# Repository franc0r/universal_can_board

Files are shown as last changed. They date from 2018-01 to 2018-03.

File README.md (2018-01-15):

# universal_can_board
Contains schematic, pcb layout and software of the francor's universal can board.

# Description
The universal board is used to control and monitor several components of a mobile robot like the motor controllers, co2 sensors, pan tilt unit, etc...

The board communicates via CAN interface. The used µC is a AVR from the Arduino Nano v2. Future more this board is based on an Arduino, so the Arduino IDE can be used to programm the board.

# Requirements
## Motor Controller
The BLD300B motor controller is used to drive the Robot Morty. This controller must be controlled and monitored by the board. For this following inputs and outputs are required.

* Input
  * An analog to measure current voltage of the motor controller.
  * An analog to measure current current of the motor controller.
  * Three digital to get the hall sensors of the hub motor wheels.
  * An digital to get the speed ticks from the motor controller.
* Output
  * An PWM to set the motor power.
  * An digital to set the rotation direction.
  * An digital to enable/disable the break.
  * An digital to enable/disable the motor controller.
  
## CO2 Sensor
The universal board should be able to measure the CO2 sensor and publish the values via CAN.

* Input
  * An analog to measure the current CO2 concentration.
  
* Output
  * An digital to indicate a high CO2 concentration. (drive a LED).

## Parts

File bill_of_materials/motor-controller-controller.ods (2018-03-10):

IC1 | ATMEGA328P-A | TQFP32 | https://www.reichelt.de/?ARTICLE=121830&PROVID=2788 | 1,4
U1 | FT232RL | SSOP28 | https://www.reichelt.de/?ACTION=3;ARTICLE=64399;SEARCH=ft232rl | 3,6
U2 | LM1117-5.0 | SOT-223 | https://www.reichelt.de/?ACTION=3;ARTICLE=109330;SEARCH=lm1117 | 0,86
U3 | MCP2515 | TSSOP-20 | https://www.reichelt.de/?ACTION=3;ARTICLE=168468;SEARCH=mcp2515 | 2,15
U4 | MCP2551 | SOIC-8 | https://www.reichelt.de/?ACTION=3;ARTICLE=90069;SEARCH=mcp2551 | 1,25
D4 | B2100-13-F | SMB | https://www.reichelt.de/?ACTION=3;ARTICLE=216722;SEARCH=b2100-13 | 0,28
D13 | B2100-13-F | SMB | https://www.reichelt.de/?ACTION=3;ARTICLE=216722;SEARCH=b2100-13 | 0,28
D14 | B2100-13-F | SMB | https://www.reichelt.de/?ACTION=3;ARTICLE=216722;SEARCH=b2100-13 | 0,28
P1 | USB Mini B | USB_OTG | https://www.reichelt.de/USB-Einbauverbinder/USB-BWM-SMD/3/index.html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 | 0,28
Y1 | Quarz 16MHz | 3x5 mm | https://www.reichelt.de/Quarze-SMD-Keramikgehaeuse/16-000000-MJ/3/index.html?ACTION=3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 | 0,9
Y2 | Quarz 16MHz | 3x5 mm | https://www.reichelt.de/Quarze-SMD-Keramikgehaeuse/16-000000-MJ/3/index.html?ACTION=3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 | 0,9
C21 | 10u 16V | 1210 | https://www.reichelt.de/Vielschicht-SMD-G1210/KEM-Y5V1210-10U/3/index.html?ACTION=3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 | 0,16
C1 | 100nF | 805 | https://www.reichelt.de/Vielschicht-SMD-G0805/KEM-X7R0805-100N/3/index.html?ACTION=3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 | 0,02
C3 | 100nF | 805 | https://www.reichelt.de/Vielschicht-SMD-G0805/KEM-X7R0805-100N/3/index.html?ACTION=3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 | 0,02
C4 | 100nF | 805 | https://www.reichelt.de/Vielschicht-SMD-G0805/KEM-X7R0805-100N/3/index.html?ACTION=3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 | 0,02
C5 | 100nF | 805 | https://www.reichelt.de/Vielschicht-SMD-G0805/KEM-X7R0805-100N/3/index.html?ACTION=3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 | 0,02
C6 | 100nF | 805 | https://www.reichelt.de/Vielschicht-SMD-G0805/KEM-X7R0805-100N/3/index.html?ACTION=3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 | 0,02
C22 | 100nF | 805 | https://www.reichelt.de/Vielschicht-SMD-G0805/KEM-X7R0805-100N/3/index.html?ACTION=3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 | 0,02
C23 | 100nF | 805 | https://www.reichelt.de/Vielschicht-SMD-G0805/KEM-X7R0805-100N/3/index.html?ACTION=3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 | 0,02
C24 | 100nF | 805 | https://www.reichelt.de/Vielschicht-SMD-G0805/KEM-X7R0805-100N/3/index.html?ACTION=3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 | 0,02
C25 | 100nF | 805 | https://www.reichelt.de/Vielschicht-SMD-G0805/KEM-X7R0805-100N/3/index.html?ACTION=3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 | 0,02
C26 | 100nF | 805 | https://www.reichelt.de/Vielschicht-SMD-G0805/KEM-X7R0805-100N/3/index.html?ACTION=3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 | 0,02
C27 | 100nF | 805 | https://www.reichelt.de/Vielschicht-SMD-G0805/KEM-X7R0805-100N/3/index.html?ACTION=3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 | 0,02
C9 | 4u7 | 1210 | https://www.reichelt.de/Vielschicht-SMD-G1210/KEM-X7R1210-4-7U/3/index.html?ACTION=3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 | 0,28
C20 | 4u7 | 1210 | https://www.reichelt.de/Vielschicht-SMD-G1210/KEM-X7R1210-4-7U/3/index.html?ACTION=3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 | 0,28
D5 | BAT54S | SOT-23 | https://www.reichelt.de/BA-BAY-BB-Dioden/BAT-54S-SMD/3/index.html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 | 0,04
D6 | BAT54S | SOT-23 | https://www.reichelt.de/BA-BAY-BB-Dioden/BAT-54S-SMD/3/index.html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 | 0,04
D7 | BAT54S | SOT-23 | https://www.reichelt.de/BA-BAY-BB-Dioden/BAT-54S-SMD/3/index.html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 | 0,04
D8 | BAT54S | SOT-23 | https://www.reichelt.de/BA-BAY-BB-Dioden/BAT-54S-SMD/3/index.html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 | 0,04
D9 | BAT54S | SOT-23 | https://www.reichelt.de/BA-BAY-BB-Dioden/BAT-54S-SMD/3/index.html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 | 0,04
D10 | BAT54S | SOT-23 | https://www.reichelt.de/BA-BAY-BB-Dioden/BAT-54S-SMD/3/index.html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 | 0,04
D11 | BAT54S | SOT-23 | https://www.reichelt.de/BA-BAY-BB-Dioden/BAT-54S-SMD/3/index.html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 | 0,04
D12 | BAT54S | SOT-23 | https://www.reichelt.de/BA-BAY-BB-Dioden/BAT-54S-SMD/3/index.html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 | 0,04
R7 | 220R | 805 | https://www.reichelt.de/SMD-0805-von-0-bis-910-Ohm/SMD-0805-220/3/index.html?ACTION=3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 | 0,03
R8 | 220R | 805 | https://www.reichelt.de/SMD-0805-von-0-bis-910-Ohm/SMD-0805-220/3/index.html?ACTION=3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 | 0,03
R9 | 220R | 805 | https://www.reichelt.de/SMD-0805-von-0-bis-910-Ohm/SMD-0805-220/3/index.html?ACTION=3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 | 0,03
R10 | 220R | 805 | https://www.reichelt.de/SMD-0805-von-0-bis-910-Ohm/SMD-0805-220/3/index.html?ACTION=3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 | 0,03
R11 | 220R | 805 | https://www.reichelt.de/SMD-0805-von-0-bis-910-Ohm/SMD-0805-220/3/index.html?ACTION=3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 | 0,03
R12 | 220R | 805 | https://www.reichelt.de/SMD-0805-von-0-bis-910-Ohm/SMD-0805-220/3/index.html?ACTION=3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 | 0,03
R13 | 220R | 805 | https://www.reichelt.de/SMD-0805-von-0-bis-910-Ohm/SMD-0805-220/3/index.html?ACTION=3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 | 0,03
R14 | 220R | 805 | https://www.reichelt.de/SMD-0805-von-0-bis-910-Ohm/SMD-0805-220/3/index.html?ACTION=3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 | 0,03
R1 | 1k | 805 | https://www.reichelt.de/SMD-0805-von-1-bis-910-kOhm/RND-0805-5-5-1K/3/index.html?ACTION=3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 | 0,02
R2 | 1k | 805 | https://www.reichelt.de/SMD-0805-von-1-bis-910-kOhm/RND-0805-5-5-1K/3/index.html?ACTION=3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 | 0,02
R3 | 1k | 805 | https://www.reichelt.de/SMD-0805-von-1-bis-910-kOhm/RND-0805-5-5-1K/3/index.html?ACTION=3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 | 0,02
R4 | 1k | 805 | https://www.reichelt.de/SMD-0805-von-1-bis-910-kOhm/RND-0805-5-5-1K/3/index.html?ACTION=3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 | 0,02
R5 | 1k | 805 | https://www.reichelt.de/SMD-0805-von-1-bis-910-kOhm/RND-0805-5-5-1K/3/index.html?ACTION=3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 | 0,02
R6 | 1k | 805 | https://www.reichelt.de/SMD-0805-von-1-bis-910-kOhm/RND-0805-5-5-1K/3/index.html?ACTION=3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 | 0,02
R15 | 1k | 805 | https://www.reichelt.de/SMD-0805-von-1-bis-910-kOhm/RND-0805-5-5-1K/3/index.html?ACTION=3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 | 0,02
R16 | 120R | 805 | https://www.reichelt.de/SMD-0805-von-0-bis-910-Ohm/SMD-0805-120/3/index.html?ACTION=3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 | 0,03

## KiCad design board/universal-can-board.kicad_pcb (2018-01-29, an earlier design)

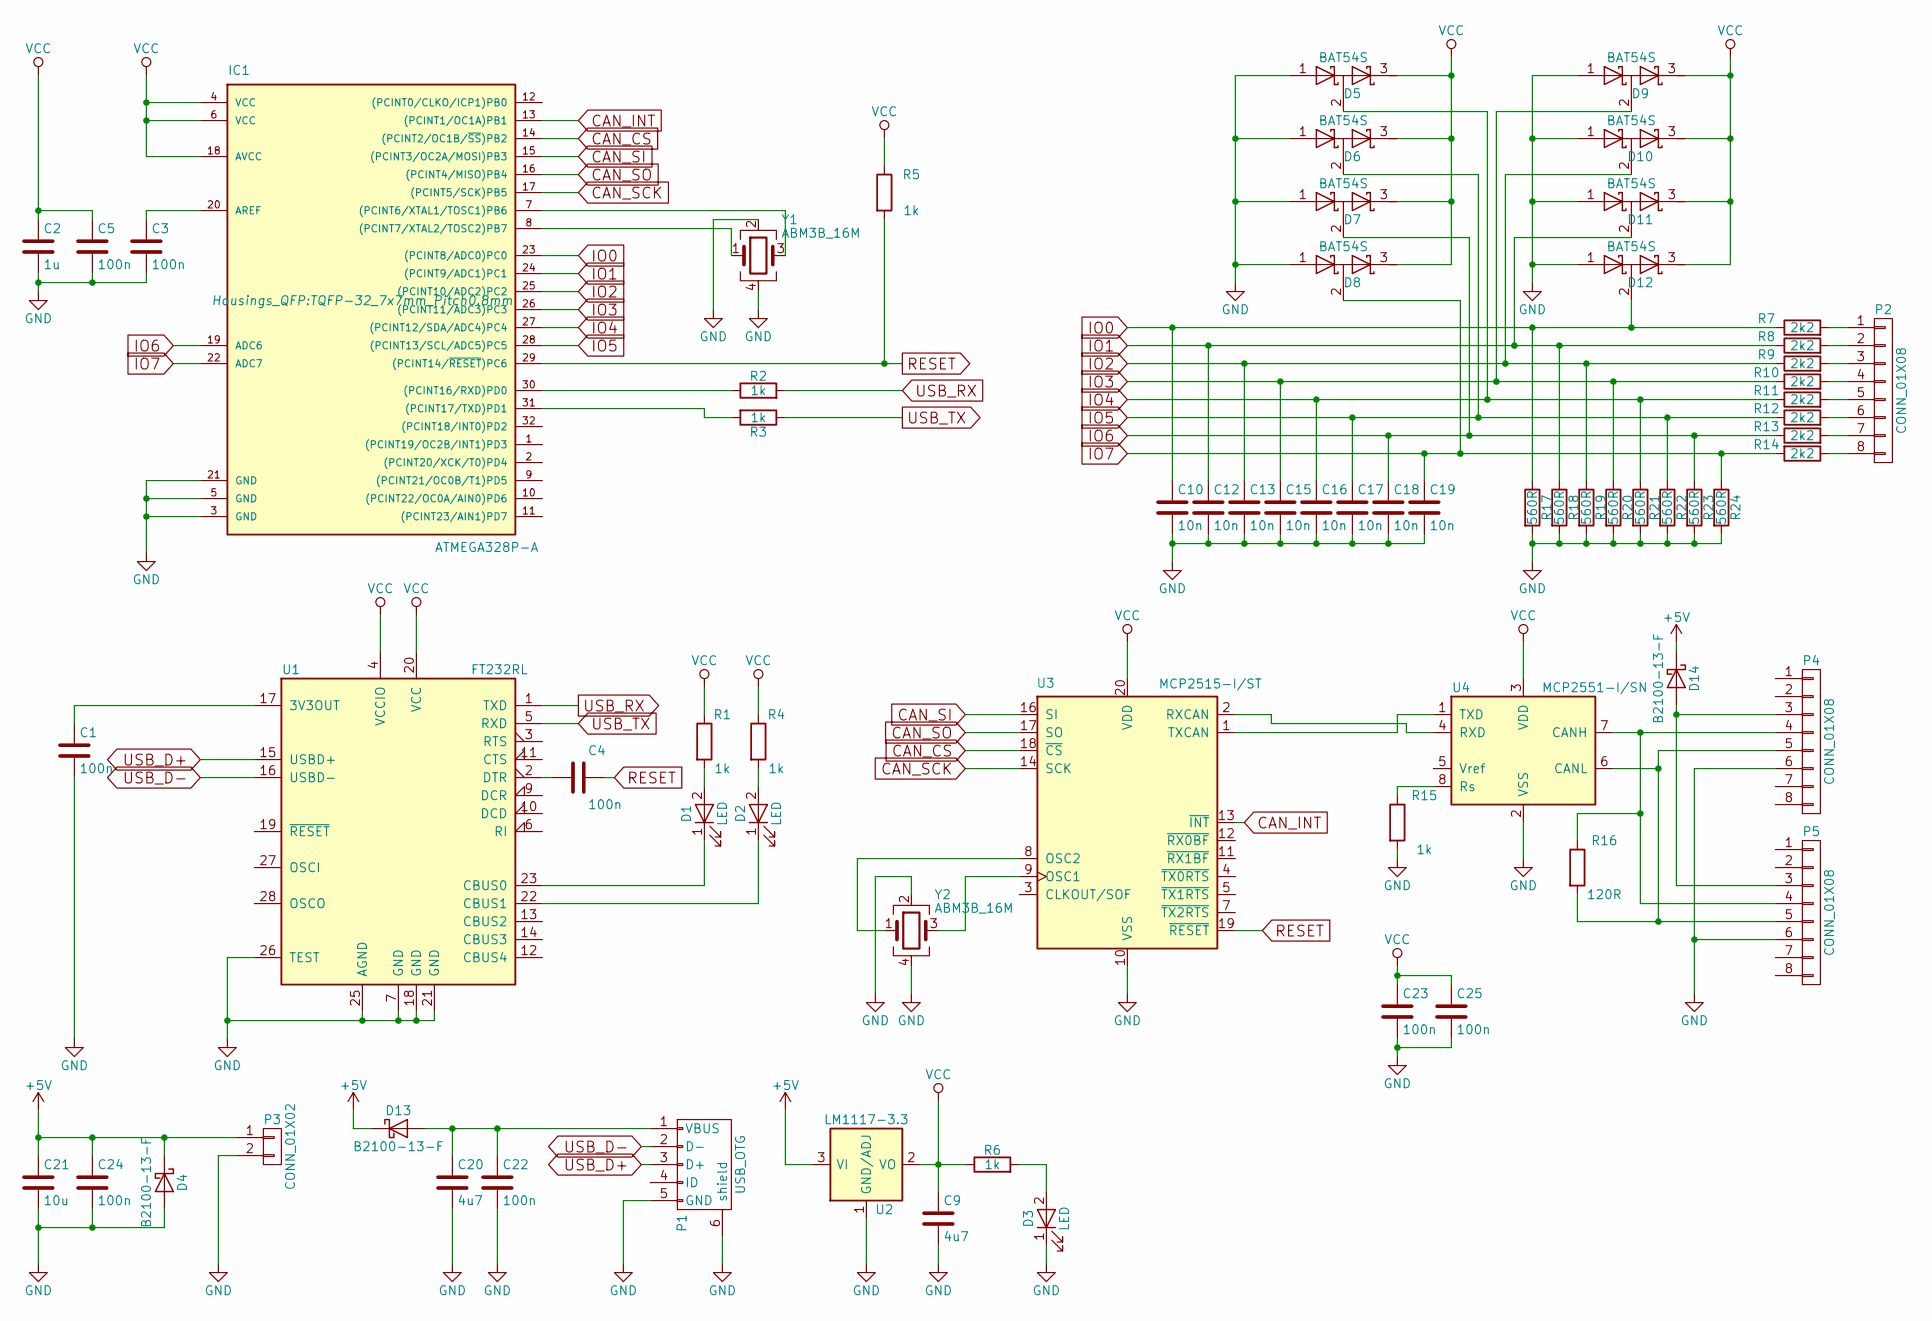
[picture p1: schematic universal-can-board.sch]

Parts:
C1, C3, C4, C5, C22, C23, C24, C25: 100n; C_0805
C2: 1u; C_0805
C9, C20: 4u7; C_1210
C10, C12, C13, C15, C16, C17, C18, C19: 10n; C_0805
C21: 10u; C_1210
D1, D2, D3: LED; LED_0805
D4, D13, D14: B2100-13-F; SMB_Standard
D5, D6, D7, D8, D9, D10, D11, D12: BAT54S; SOT-23
IC1: ATMEGA328P-A; TQFP-32_7x7mm_Pitch0.8mm
P1: USB_OTG; USB_Mini-B_Lumber_2486_Horizontal
P2: CONN_01X08; PhoenixContact_MSTBVA-G_08x5.08mm_Vertical
P3: CONN_01X02; PhoenixContact_MSTBVA-G_02x5.08mm_Vertical
P4, P5: CONN_01X08; RJ45_8
R1, R2, R3, R4, R5, R6, R15: 1k; R_0805
R7, R8, R9, R10, R11, R12, R13, R14: 2k2; R_0805
R16: 120R; R_0805
R17, R18, R19, R20, R21, R22, R23, R24: 560R; R_0805
U1: FT232RL; SSOP-28_5.3x10.2mm_Pitch0.65mm
U2: LM1117-3.3; SOT-223
U3: MCP2515-I/ST; TSSOP-20_4.4x6.5mm_Pitch0.65mm
U4: MCP2551-I/SN; SOIC-8_3.9x4.9mm_Pitch1.27mm
Y1, Y2: ABM3B_16M; Crystal_SMD_5032_4Pads

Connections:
+5V: C21.1, C24.1, D4.1 (K), D13.1 (K), D14.1 (K), P3.1, U2.3 (VI)
CAN_CS: IC1.14 ((PCINT2/OC1B/~SS~)PB2), U3.18 (~CS)
CAN_INT: IC1.13 ((PCINT1/OC1A)PB1), U3.13 (~INT)
CAN_SCK: IC1.17 ((PCINT5/SCK)PB5), U3.14 (SCK)
CAN_SI: IC1.15 ((PCINT3/OC2A/MOSI)PB3), U3.16 (SI)
CAN_SO: IC1.16 ((PCINT4/MISO)PB4), U3.17 (SO)
GND: C1.2, C2.2, C3.2, C5.2, C9.2, C10.2, C12.2, C13.2, C15.2, C16.2, C17.2, C18.2, C19.2, C20.2, C21.2, C22.2, C23.2, C24.2, C25.2, D3.1 (K), D4.2 (A), D5.1 (A), D6.1 (A), D7.1 (A), D8.1 (A), D9.1 (A), D10.1 (A), D11.1 (A), D12.1 (A), IC1.3 (GND), IC1.5 (GND), IC1.21 (GND), P1.5 (GND), P1.6 (shield), P3.2, P4.6, P5.6, R15.2, R17.2, R18.2, R19.2, R20.2, R21.2, R22.2, R23.2, R24.2, U1.7 (GND), U1.18 (GND), U1.21 (GND), U1.25 (AGND), U1.26 (TEST), U2.1 (GND/ADJ), U3.10 (VSS), U4.2 (VSS), Y1.2, Y1.4, Y2.2, Y2.4
IO0: C10.1, D12.2 (common), IC1.23 ((PCINT8/ADC0)PC0), R7.1, R17.1
IO1: C12.1, D11.2 (common), IC1.24 ((PCINT9/ADC1)PC1), R8.1, R18.1
IO2: C13.1, D10.2 (common), IC1.25 ((PCINT10/ADC2)PC2), R9.1, R19.1
IO3: C15.1, D9.2 (common), IC1.26 ((PCINT11/ADC3)PC3), R10.1, R20.1
IO4: C16.1, D5.2 (common), IC1.27 ((PCINT12/SDA/ADC4)PC4), R11.1, R21.1
IO5: C17.1, D6.2 (common), IC1.28 ((PCINT13/SCL/ADC5)PC5), R12.1, R22.1
IO6: C18.1, D7.2 (common), IC1.19 (ADC6), R13.1, R23.1
IO7: C19.1, D8.2 (common), IC1.22 (ADC7), R14.2, R24.1
unnamed: C1.1, U1.17 (3V3OUT)
unnamed: C3.1, IC1.20 (AREF)
unnamed: C4.2, U1.2 (DTR)
unnamed: C20.1, C22.1, D13.2 (A), P1.1 (VBUS)
unnamed: D1.1 (K), U1.23 (CBUS0)
unnamed: D1.2 (A), R1.2
unnamed: D2.1 (K), U1.22 (CBUS1)
unnamed: D2.2 (A), R4.2
unnamed: D3.2 (A), R6.2
unnamed: D14.2 (A), P4.3, P5.3
unnamed: IC1.7 ((PCINT6/XTAL1/TOSC1)PB6), Y1.3
unnamed: IC1.8 ((PCINT7/XTAL2/TOSC2)PB7), Y1.1
unnamed: IC1.30 ((PCINT16/RXD)PD0), R2.1
unnamed: IC1.31 ((PCINT17/TXD)PD1), R3.2
unnamed: P2.1, R7.2
unnamed: P2.2, R8.2
unnamed: P2.3, R9.2
unnamed: P2.4, R10.2
unnamed: P2.5, R11.2
unnamed: P2.6, R12.2
unnamed: P2.7, R13.2
unnamed: P2.8, R14.1
unnamed: P4.4, P5.4, R16.1, U4.7 (CANH)
unnamed: P4.5, P5.5, R16.2, U4.6 (CANL)
unnamed: R15.1, U4.8 (Rs)
unnamed: U3.1 (TXCAN), U4.1 (TXD)
unnamed: U3.2 (RXCAN), U4.4 (RXD)
unnamed: U3.8 (OSC2), Y2.1
unnamed: U3.9 (OSC1), Y2.3
RESET: C4.1, IC1.29 ((PCINT14/~RESET~)PC6), R5.2, U3.19 (~RESET)
USB_D+: P1.3 (D+), U1.15 (USBD+)
USB_D-: P1.2 (D-), U1.16 (USBD-)
USB_RX: R2.2, U1.1 (TXD)
USB_TX: R3.1, U1.5 (RXD)
VCC: C2.1, C5.1, C9.1, C23.1, C25.1, D5.3 (K), D6.3 (K), D7.3 (K), D8.3 (K), D9.3 (K), D10.3 (K), D11.3 (K), D12.3 (K), IC1.4 (VCC), IC1.6 (VCC), IC1.18 (AVCC), R1.1, R4.1, R5.1, R6.1, U1.4 (VCCIO), U1.20 (VCC), U2.2 (VO), U2.4 (VO), U3.20 (VDD), U4.3 (VDD)

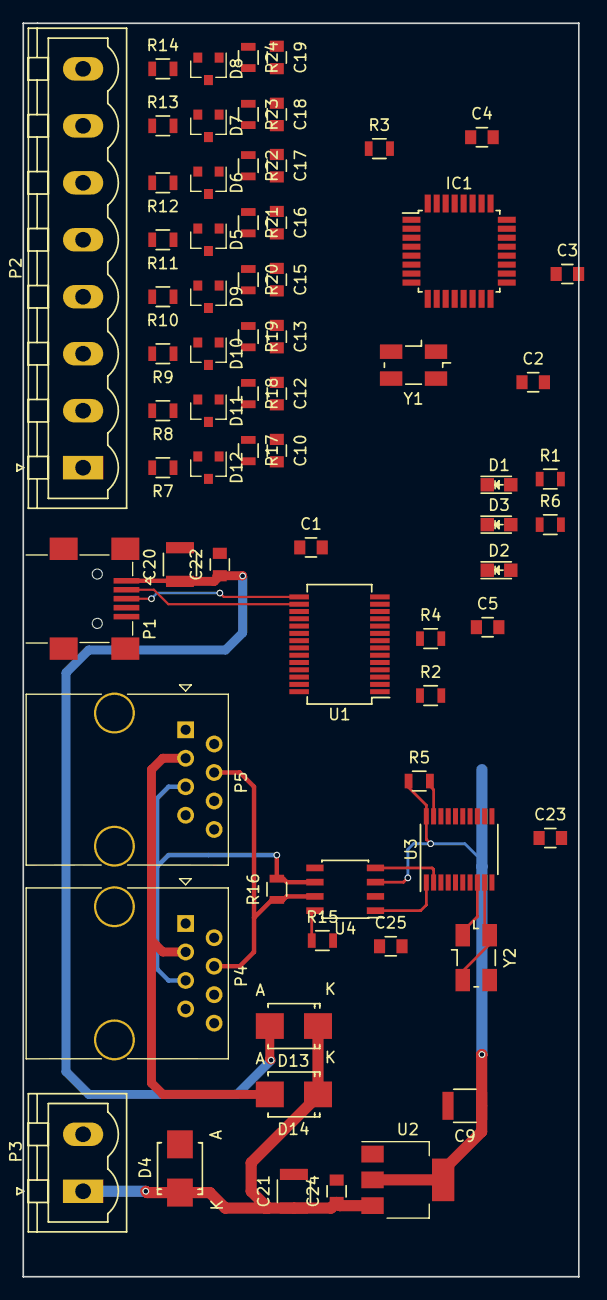
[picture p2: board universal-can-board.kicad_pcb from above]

Board: 2 copper layers, 49.5 x 111.8 mm, 70 parts (0 on the bottom side), 50 nets.

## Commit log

2018-01-28 Created schematic of the board, including µC, USB FTDI and CAN controller + transreceiver. Review required.
    [universal-can-board.kicad_pcb, universal-can-board.sch]
2018-01-28 Added values to the board schematic.
    [universal-can-board.sch]
2018-01-28 Removed conflicts in board schematic.
    [universal-can-board.sch]
2018-01-29 Improved input circuit protection. Started with first version of the layout.
    [universal-can-board.kicad_pcb, universal-can-board.sch]
2018-02-07 Just saved new pcb layout try.
    [universal-can-board-v1.1.kicad_pcb]
2018-02-08 Moved on with the layout.
    [universal-can-board-v1.1.kicad_pcb]
2018-02-11 Routing of board v1.1
    [universal-can-board-v1.1.kicad_pcb, universal-can-board.sch]
2018-02-11 Routing of PCB v1.1. All parts are placed now.
    [universal-can-board-v1.1.kicad_pcb]
2018-02-15 Updated board layout.
    [universal-can-board-v1.1.kicad_pcb, universal-can-board.sch]
2018-03-05 Added last missing parts and changed some routings.
    [universal-can-board-v1.1.kicad_pcb, universal-can-board.sch]
2018-03-05 Added two mounting holes to the pcb.
    [universal-can-board-v1.1.kicad_pcb]
2018-03-05 Flipped input filter C (CAN) from top to bottom.
    [universal-can-board-v1.1.kicad_pcb, universal-can-board.sch]
2018-03-10 Added material bill for the motorcontroller controller.
    [motor-controller-controller.ods]
